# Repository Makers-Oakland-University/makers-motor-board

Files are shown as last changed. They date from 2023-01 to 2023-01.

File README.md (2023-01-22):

# Makers @ OU General Purpose Motor Board

Makers Motor Board

The Makers @ OU motor board is meant to serve as a general-purpose robot base for all kinds of projects. 
The board utilizes the ESP32 Devkit 1, along with an L293D H-Bridge driver. 
The LM7805 voltage regulator enables the board to be powered from any supply between 4.5V and 30V. 
The input voltage can be used directly to drive the motor, or the 5V power rail can be used through selection through the header. 

This repo contains the KiCad EDA files for the board, gerber production files, the board schematic in PDF format, and a .step file to aid CAD design. 

# ESP32 Pin Connections

The following pins on the ESP32 are connected to the motor driver:

- IO26 -> Driver 1A
- IO27 -> Driver 2A
- IO23 -> Driver 3A
- IO25 -> Driver 4A
- IO32 -> Driver 1,2EN
- IO33 -> Driver 3,4EN

# BOM 
This section provides a list of components used by this board, and some amazon links that can be used to acquire them. 

- [ESP32 DevKit V1](https://www.amazon.com/ESP32-WROOM-32-Development-ESP-32S-Bluetooth-Arduino/dp/B084KWNMM4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)
- [L293D Motor Driver](https://www.amazon.com/BOJACK-16-pin-Stepper-Drivers-Controllers/dp/B09NBQVYLL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)
- [LM7805 Voltage Regulator](https://www.amazon.com/BOJACK-Regulator-Integrated-Circuits-Regulators/dp/B07VRS9HW4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)
- [2 Position 5mm Pitch Terminal Blocks](https://www.amazon.com/DIYhz-green-Terminal-Connector-Arduino/dp/B0774YRVVX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)
- [Standard Header Jumpers (only need 1 per board)](https://www.amazon.com/uxcell-100pcs-Standard-Circuit-Connection/dp/B08Y7Y9LKV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)

Any electrolytic capacitor can be used provided it's voltage rating is above the input voltage present at PWR IN

# Acknoledgements 
This repo uses Victor Lamoine's [ESP32 Devkit V1 Symbol and Footprint](https://gitlab.com/VictorLamoine/kicad).

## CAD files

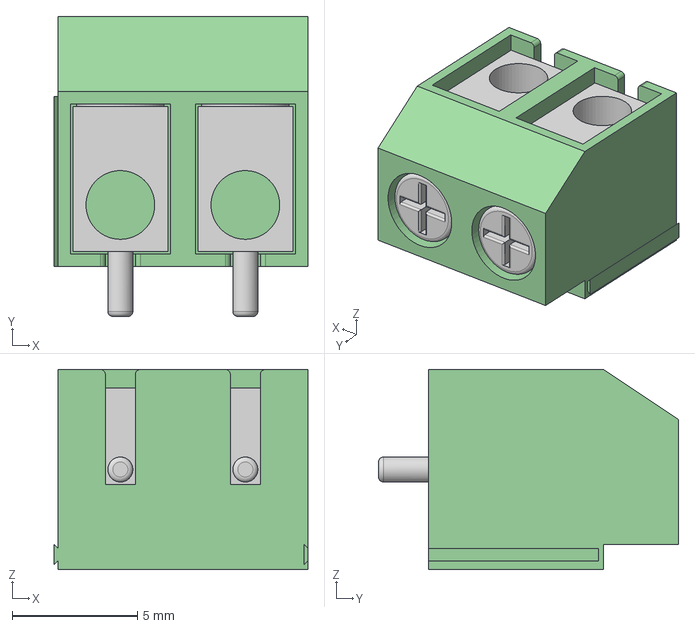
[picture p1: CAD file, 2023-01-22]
KiCad Files/imports/Screw Terminal Block 5mm 2-way.step
10.2 x 12.0 x 8.00 mm

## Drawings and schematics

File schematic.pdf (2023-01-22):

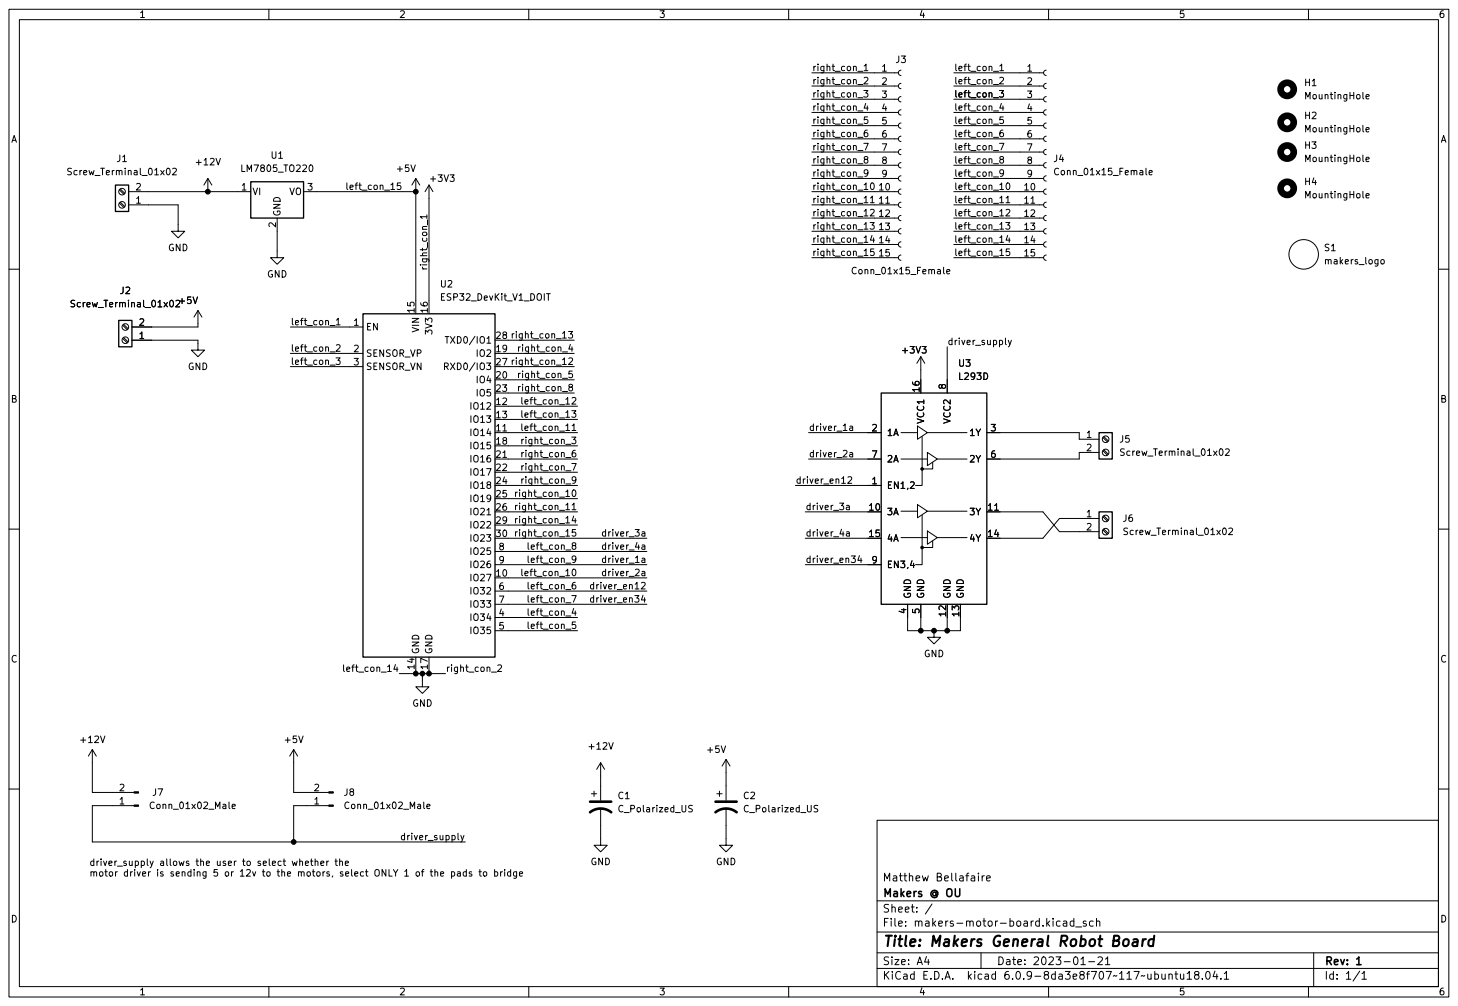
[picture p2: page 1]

driver_supply allows the user to select whether the
motor driver is sending 5 or 12v to the motors, select ONLY 1 of the pads to bridge

File: makers-motor-board.kicad_sch Sheet: / Makers @ OU Matthew Bellafaire

Id: 1/1 Title: Makers General Robot Board

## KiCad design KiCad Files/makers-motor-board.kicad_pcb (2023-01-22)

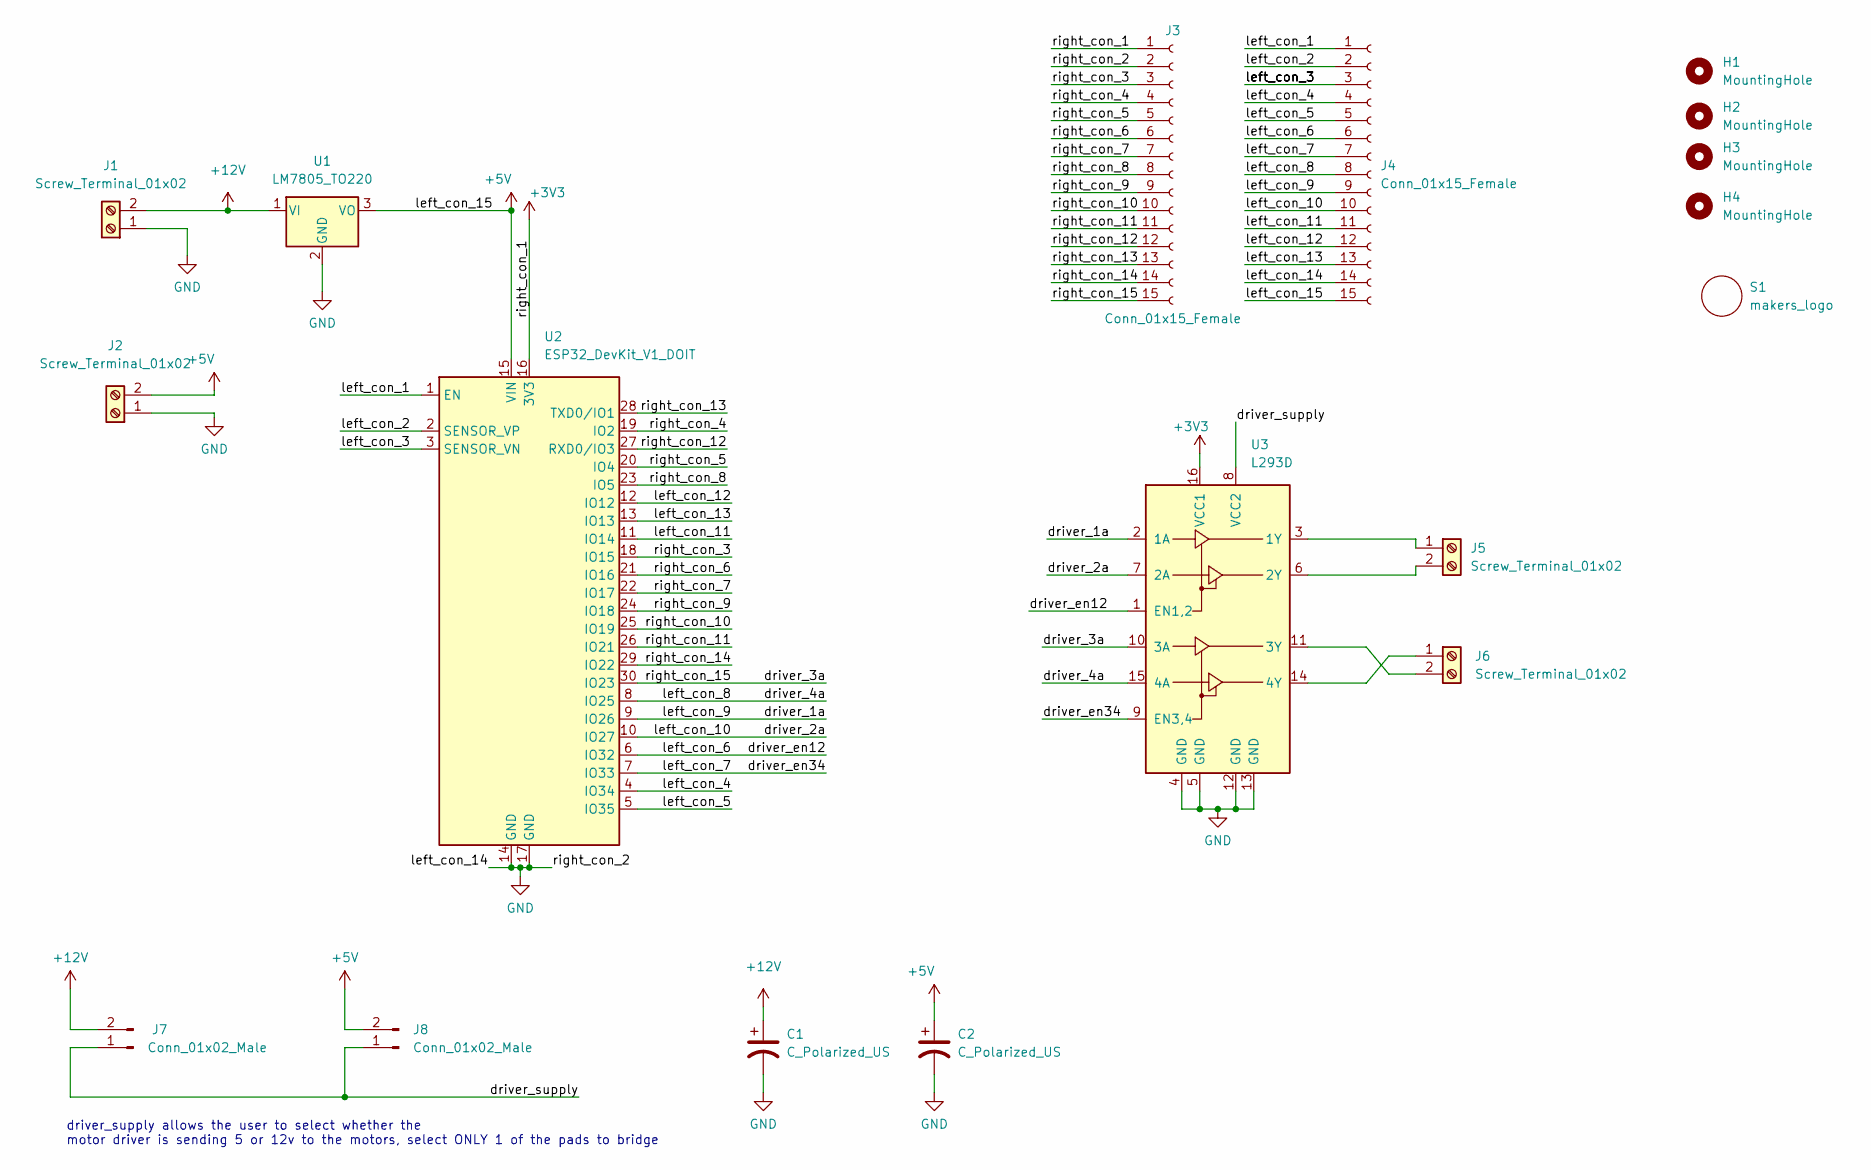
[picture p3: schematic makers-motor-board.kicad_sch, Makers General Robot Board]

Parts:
C1, C2: C_Polarized_US; CP_Radial_D8.0mm_P3.50mm
H1, H2, H3, H4: MountingHole; MountingHole_3.2mm_M3_Pad
J1, J2, J5, J6: Screw_Terminal_01x02; terminal_block_5mm
J3, J4: Conn_01x15_Female; PinSocket_1x15_P2.54mm_Vertical
J7, J8: Conn_01x02_Male; PinHeader_1x02_P2.54mm_Vertical
S1: makers_logo
U1: LM7805_TO220; TO-220-3_Horizontal_TabDown
U2: ESP32_DevKit_V1_DOIT; esp32_devkit_v1_doit
U3: L293D; DIP-16_W7.62mm

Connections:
+3V3: J3.1, U2.16 (3V3), U3.16 (VCC1)
+5V: C2.1, J2.2, J4.15, J8.2, U1.3 (VO), U2.15 (VIN)
+12V: C1.1, J1.2, J7.2, U1.1 (VI)
/driver_1a: J4.9, U2.9 (IO26), U3.2 (1A)
/driver_2a: J4.10, U2.10 (IO27), U3.7 (2A)
/driver_3a: J3.15, U2.30 (IO23), U3.10 (3A)
/driver_4a: J4.8, U2.8 (IO25), U3.15 (4A)
/driver_en12: J4.6, U2.6 (IO32), U3.1 (EN1,2)
/driver_en34: J4.7, U2.7 (IO33), U3.9 (EN3,4)
/driver_supply: J7.1, J8.1, U3.8 (VCC2)
/left_con_1: J4.1, U2.1 (EN)
/left_con_2: J4.2, U2.2 (SENSOR_VP)
/left_con_3: J4.3, U2.3 (SENSOR_VN)
/left_con_4: J4.4, U2.4 (IO34)
/left_con_5: J4.5, U2.5 (IO35)
/left_con_11: J4.11, U2.11 (IO14)
/left_con_12: J4.12, U2.12 (IO12)
/left_con_13: J4.13, U2.13 (IO13)
/right_con_3: J3.3, U2.18 (IO15)
/right_con_4: J3.4, U2.19 (IO2)
/right_con_5: J3.5, U2.20 (IO4)
/right_con_6: J3.6, U2.21 (IO16)
/right_con_7: J3.7, U2.22 (IO17)
/right_con_8: J3.8, U2.23 (IO5)
/right_con_9: J3.9, U2.24 (IO18)
/right_con_10: J3.10, U2.25 (IO19)
/right_con_11: J3.11, U2.26 (IO21)
/right_con_12: J3.12, U2.27 (RXD0/IO3)
/right_con_13: J3.13, U2.28 (TXD0/IO1)
/right_con_14: J3.14, U2.29 (IO22)
GND: C1.2, C2.2, J1.1, J2.1, J3.2, J4.14, U1.2 (GND), U2.14 (GND), U2.17 (GND), U3.4 (GND), U3.5 (GND), U3.12 (GND), U3.13 (GND)
unnamed: J5.1, U3.3 (1Y)
unnamed: J5.2, U3.6 (2Y)
unnamed: J6.1, U3.14 (4Y)
unnamed: J6.2, U3.11 (3Y)

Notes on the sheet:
driver_supply allows the user to select whether the motor driver is sending 5 or 12v to the motors, select ONLY 1 of the pads to bridge

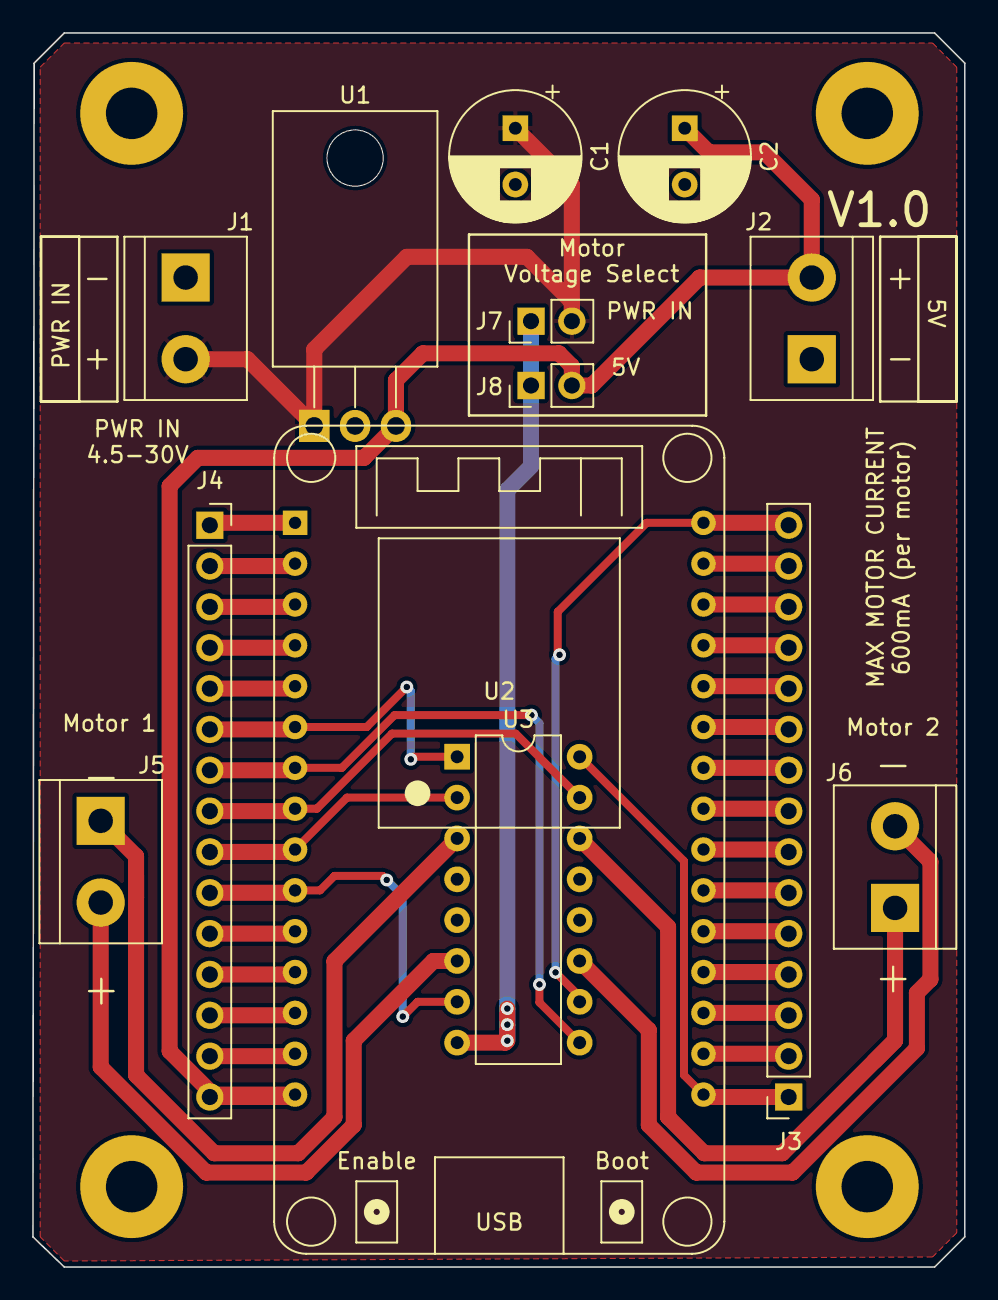
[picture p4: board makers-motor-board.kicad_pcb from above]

Board: 2 copper layers, 58.0 x 76.8 mm, 18 parts (1 on the bottom side), 35 nets.
